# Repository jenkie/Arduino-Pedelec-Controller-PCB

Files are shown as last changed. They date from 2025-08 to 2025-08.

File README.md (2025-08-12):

# Arduino-Pedelec-Controller-PCB
PCB files for the Arduino Pedelec Controller

More info see http://www.pedelecforum.de/wiki/doku.php?id=elektrotechnik:forumscontroller

Shield: [][cc-by-nc]

This work is licensed under a
[Creative Commons Attribution-NonCommercial 4.0 International License][cc-by-nc].

[][cc-by-nc]

[cc-by-nc]: https://creativecommons.org/licenses/by-nc/4.0/
[cc-by-nc-image]: https://licensebuttons.net/l/by-nc/4.0/88x31.png
[cc-by-nc-shield]: https://img.shields.io/badge/License-CC%20BY--NC%204.0-lightgrey.svg

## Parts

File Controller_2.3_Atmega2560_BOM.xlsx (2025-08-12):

Part | Part Number | Quantity | Supplier
Housing | 1593LBK | 1 | Reichelt
Screws | SBL 29065-100 | 4 | Reichelt
Washers | 16 H 942 | 4 | Buerklin
RJ45-8X | 1401749 | 2 | Conrad
Connector 2-pol | PS 25/2G WS | 4 | Reichelt
Connector 3-Pol | PS 25/3G WS | 1
Connector 4-Pin | JST XH4P ST | 2 | Reichelt
Connector 4-Pin | 452408 | 2 | Pollin
Connector 5-Pol | PS 25/5G WS | 1 | Reichelt
ISP HDR 2x3 | SL 2X50G 2,54 | 1 | Reichelt
Buzzer | SUMMER AL-60P12 | 1 | Reichelt

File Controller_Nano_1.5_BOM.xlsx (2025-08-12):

Part | Description | Package | Part Number | Quantity | Supplier
Q3 | IRFS3107PBF | TO263 | IRFS3107PBF | 1 | Farnell
IC3 | LM2576HVS-ADJ | TO263-5 | 41 S 5413 | 1 | Buerklin
IC1 | ACS712 | SO-8 | 1651975 | 1 | Farnell
Pin header | 36 Pole |  | 59 F 6960 | 1 | Buerklin
RJ45 | RJ45-8X |  | 73 F 670 | 2 | Buerklin
U$1 | PIST-151 | PIST-151 | 74 D 4854 | 1 | Buerklin
IC2 | TLV1117-50CDCY 5V Regler | SOT223 | 1755288 | 1 | Farnell
R11 | 2K Trimmer | PVZ2A202A01B00 | PVZ2A202A01B00 | 1 | Farnell
D1 | SS3H10 | SMC | 1215109 | 1 | Farnell
T1 | IRFML8244TRPBF, FET | SOT-23 | 1857298 | 1 | Farnell
C2 | 100µF 63V | E3,5-8 | 12 D 5194 | 1 | Buerklin
C3 | 470 µF 16 V | E3,5-8 | 12 D 5114 | 1 | Buerklin
C4,9 | 100µF | E2-5 | 11 D 5300 | 2 | Buerklin
Q2 | NPN with hfe > 100 | SOT-23 | BC846B | 1 | Reichelt
R2,5,10,12,13 | 11k | R1206 | 1887478 | 5 | Farnell
C1,C10 | 10µF, 63V | E2-5 | 11 D 5346 | 2 | Buerklin
D2 | 20V/1A | DO-214AC | 1611257 | 1 | Farnell
R9 | 1.25k | R1206 | CRCW12061K20FKEA | 1 | Farnell
C5,8,11 | 1µF, 25V | C0805 | 1759429 | 3 | Farnell
R1 | 470K | R1206 | 1887522 | 1 | Farnell
R3,4,6 | 1k | R1206 | 2073877 | 3 | Farnell
C6,7 | 220n, >5V | C0805 | 1759173 | 2 | Farnell
D3 | Zener 12V | SOD323-W | MM3Z12VT1G | 1 | HBE
R8,15 | 150R | R1206 | 1100169 | 2 | Farnell
R18 | 150k | R1206 | 1100249 | 1 | Farnell
R7 | 820K | R1206 | 9337636 | 1 | Farnell
Screws | SBL 29065-100 |  | SBL 29065-100 | 4 | Reichelt
Housing | 1593LBK | Hammond | 1593LBK | 1 | Buerklin
Washers |  |  | 16 H 942 | 4 | Buerklin

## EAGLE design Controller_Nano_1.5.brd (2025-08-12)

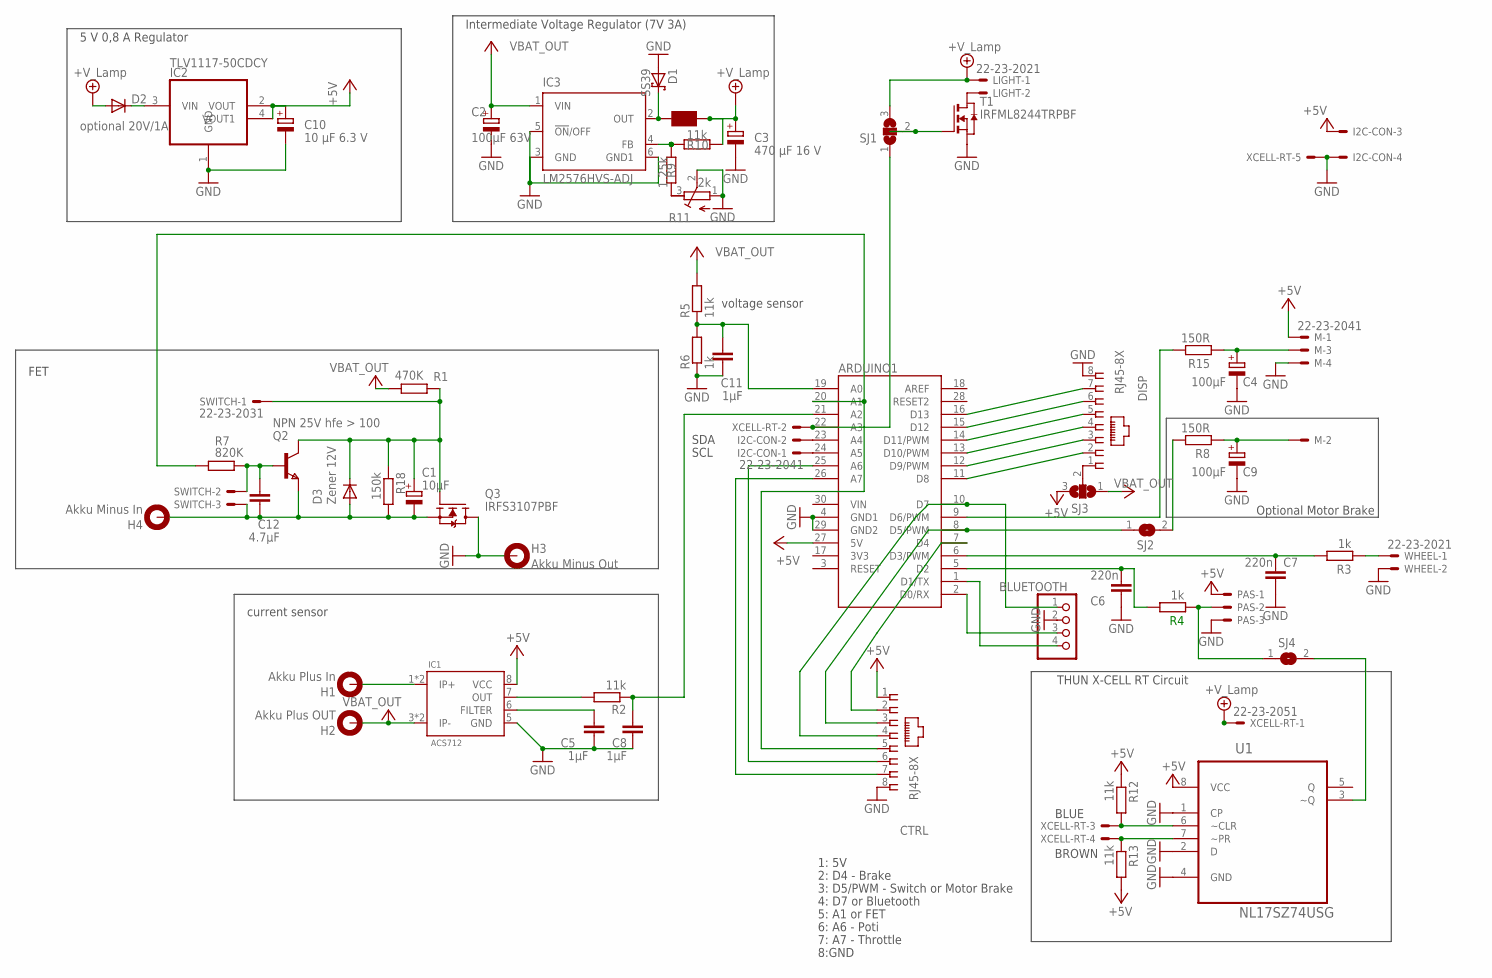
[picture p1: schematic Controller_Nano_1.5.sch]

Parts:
ARDUINO1: ARDUINO_NANO_CHECKED
BLUETOOTH: PINHD-1X4; 1X04
C1: 10µF; E2-5
C2: 100µF 63V; E3,5-8
C3: 470 µF 16 V; E3,5-8
C4, C9: 100µF; E2-5
C5, C8, C11: 1µF; C0805
C6, C7: 220n; C0805
C10: 10 µF 6.3 V; E2-5
C12: 4.7µF; C0805
CTRL: RJ45-8X; RJ45-NO-SHIELD
D1: SS39; SMC
D2: optional 20V/1A; DO-214AC
D3: Zener 12V; SOD323-W
DISP: RJ45-8X; RJ45-NO-SHIELD
H1: Akku Plus In; 2,8-PAD
H2: Akku Plus OUT; 2,8-PAD
H3: Akku Minus Out; 2,8-PAD
H4: Akku Minus In; 2,8-PAD
I2C-CON: 22-23-2041
IC1: ACS712; MARTIN-SMD-IC_SO-8
IC2: TLV1117-50CDCY; SOT223
IC3: LM2576HVS-ADJ; TO263-5
LIGHT: 22-23-2021; MPN 22-23-2021
M: 22-23-2041; MPN 22-23-2041
PAS: 22-23-2031
Q2: NPN 25V hfe > 100; SOT-23
Q3: IRFS3107PBF; TRANSISTOR-FET_TO263
R1: 470K; R1206
R2, R5, R10, R12, R13: 11k; R1206
R3, R4, R6: 1k; R1206
R7: 820K; R1206
R8, R15: 150R; R1206
R9: 1.25k; R1206
R11: 2k; RTRIM3103
R18: 150k; R1206
SJ1, SJ3: SJ2WW; SJ_2W
SJ2, SJ4: SJ
SWITCH: 22-23-2031; MPN 22-23-2031
T1: IRFML8244TRPBF; SOT-23
U1: NL17SZ74USG; SOP50P310X90-8N
U$1: PIST-151
WHEEL: 22-23-2021
XCELL-RT: 22-23-2051

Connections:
3V3: ARDUINO1.17 (3V3)
+5V: ARDUINO1.27 (5V), C10.+, CTRL.1, I2C-CON.3, IC1.8 (VCC), IC2.2 (VOUT), IC2.4 (VOUT1), M.1, PAS.1, R12.1, R13.2, SJ3.3, U1.8 (VCC)
+5V/2: C3.+, D2.A, LIGHT.1, R10.1, SJ1.3, U$1.P$2, XCELL-RT.1
GND: ARDUINO1.4 (GND1), ARDUINO1.29 (GND2), BLUETOOTH.2, C2.-, C3.-, C4.-, C5.2, C6.2, C7.2, C8.2, C9.-, C10.-, C11.2, CTRL.8, D1.A, DISP.8, H3.B2,8, I2C-CON.4, IC1.5 (GND), IC2.1 (GND), IC3.3 (GND), IC3.5 (!ON!/OFF), IC3.6 (GND1), M.4, PAS.3, Q3.2D (D), R6.1, R11.1 (E), R11.2 (S), T1.2 (S), U1.1 (CP), U1.2 (D), U1.4 (GND), WHEEL.2, XCELL-RT.5
unnamed: ARDUINO1.24 (A5), I2C-CON.1
unnamed: ARDUINO1.23 (A4), I2C-CON.2
unnamed: ARDUINO1.20 (A1), CTRL.5, R7.2
unnamed: ARDUINO1.16 (D13), DISP.7
unnamed: ARDUINO1.15 (D12), DISP.6
unnamed: ARDUINO1.14 (D11/PWM), DISP.5
unnamed: ARDUINO1.13 (D10/PWM), DISP.4
unnamed: ARDUINO1.12 (D9/PWM), DISP.3
unnamed: ARDUINO1.9 (D6/PWM), R15.2
unnamed: IC3.4 (FB), R9.2, R10.2
unnamed: LIGHT.2, T1.1 (D)
unnamed: C1.-, C12.2, D3.A, H4.B2,8, Q2.2 (E), Q3.3S (S), R18.2, SWITCH.3
unnamed: C1.+, D3.C, Q2.1 (C), Q3.1G (G), R1.2, R18.1, SWITCH.1
unnamed: R3.1, WHEEL.1
unnamed: D1.C, IC3.2 (OUT), U$1.P$1
unnamed: C5.1, IC1.6 (FILTER)
unnamed: ARDUINO1.19 (A0), C11.1, R5.1, R6.2
unnamed: ARDUINO1.22 (A3), SJ1.1, XCELL-RT.2
unnamed: ARDUINO1.7 (D4), CTRL.2
unnamed: ARDUINO1.8 (D5/PWM), CTRL.3, SJ2.1
unnamed: ARDUINO1.10 (D7), BLUETOOTH.1, CTRL.4
unnamed: C12.1, Q2.3 (B), R7.1, SWITCH.2
unnamed: ARDUINO1.11 (D8), DISP.2
unnamed: ARDUINO1.5 (D2), C6.1, R4.2
unnamed: IC1.7 (OUT), R2.2
unnamed: ARDUINO1.2 (D0/RX), BLUETOOTH.3
unnamed: ARDUINO1.25 (A6), CTRL.6
unnamed: ARDUINO1.26 (A7), CTRL.7
unnamed: ARDUINO1.1 (D1/TX), BLUETOOTH.4
unnamed: C9.+, M.2, R8.1
unnamed: C4.+, M.3, R15.1
unnamed: PAS.2, R4.1, SJ4.1
unnamed: ARDUINO1.6 (D3/PWM), C7.1, R3.2
unnamed: DISP.1, SJ3.2
unnamed: ARDUINO1.21 (A2), C8.1, R2.1
unnamed: SJ1.2, T1.3 (G)
unnamed: D2.C, IC2.3 (VIN)
unnamed: R8.2, SJ2.2
unnamed: R9.1, R11.3 (A)
unnamed: R12.2, U1.6 (~CLR), XCELL-RT.3
unnamed: R13.1, U1.7 (~PR), XCELL-RT.4
unnamed: SJ4.2, U1.3 (~Q)
VBAT_IN: H1.B2,8, IC1.1 (IP+), IC1.2 (IP+)
VBAT_OUT: C2.+, H2.B2,8, IC1.3 (IP-), IC1.4 (IP-), IC3.1 (VIN), R1.1, R5.2, SJ3.1

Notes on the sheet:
voltage sensor
current sensor
Intermediate Voltage Regulator (7V 3A)
1: 5V
2: D4 - Brake
3: D5/PWM - Switch or Motor Brake
4: D7 or Bluetooth
5: A1 or FET
6: A6 - Poti
7: A7 - Throttle
8:GND
SDA
SCL
FET
Optional Motor Brake
5 V 0,8 A Regulator
BLUE
BROWN
THUN X-CELL RT Circuit

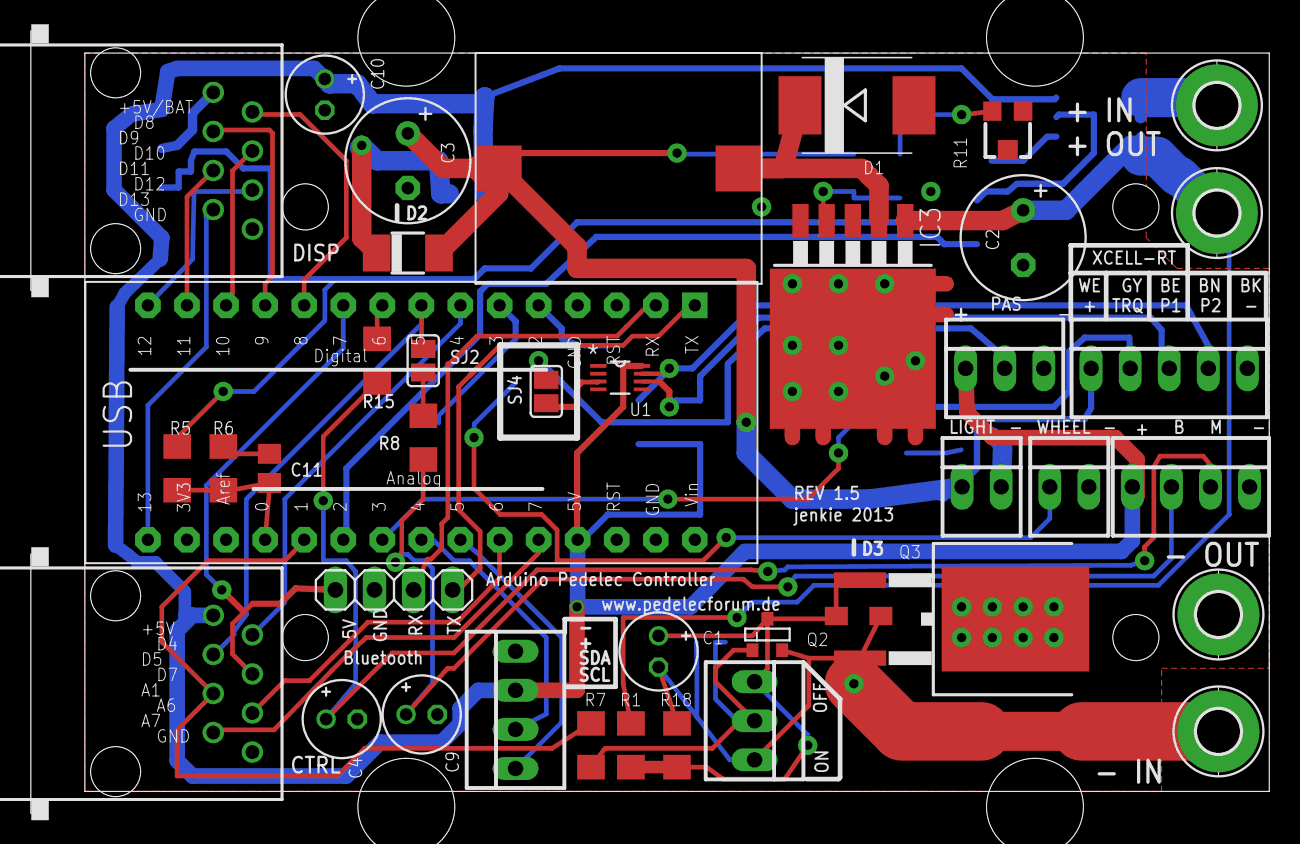
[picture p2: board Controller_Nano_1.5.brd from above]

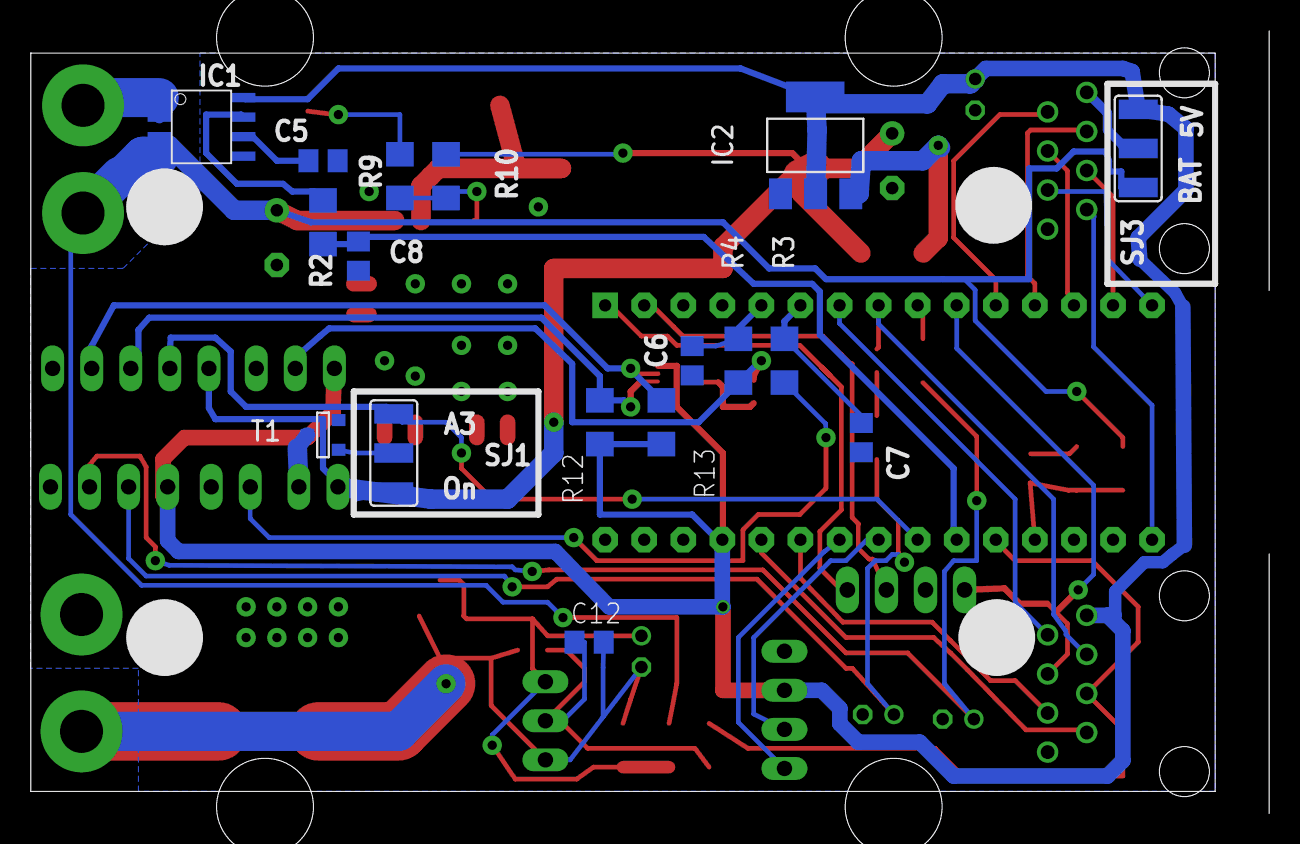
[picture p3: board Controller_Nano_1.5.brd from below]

Board: 2 copper layers, 80.5 x 50.9 mm, 58 parts (17 on the bottom side), 47 nets.

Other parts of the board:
U$2: 1593L

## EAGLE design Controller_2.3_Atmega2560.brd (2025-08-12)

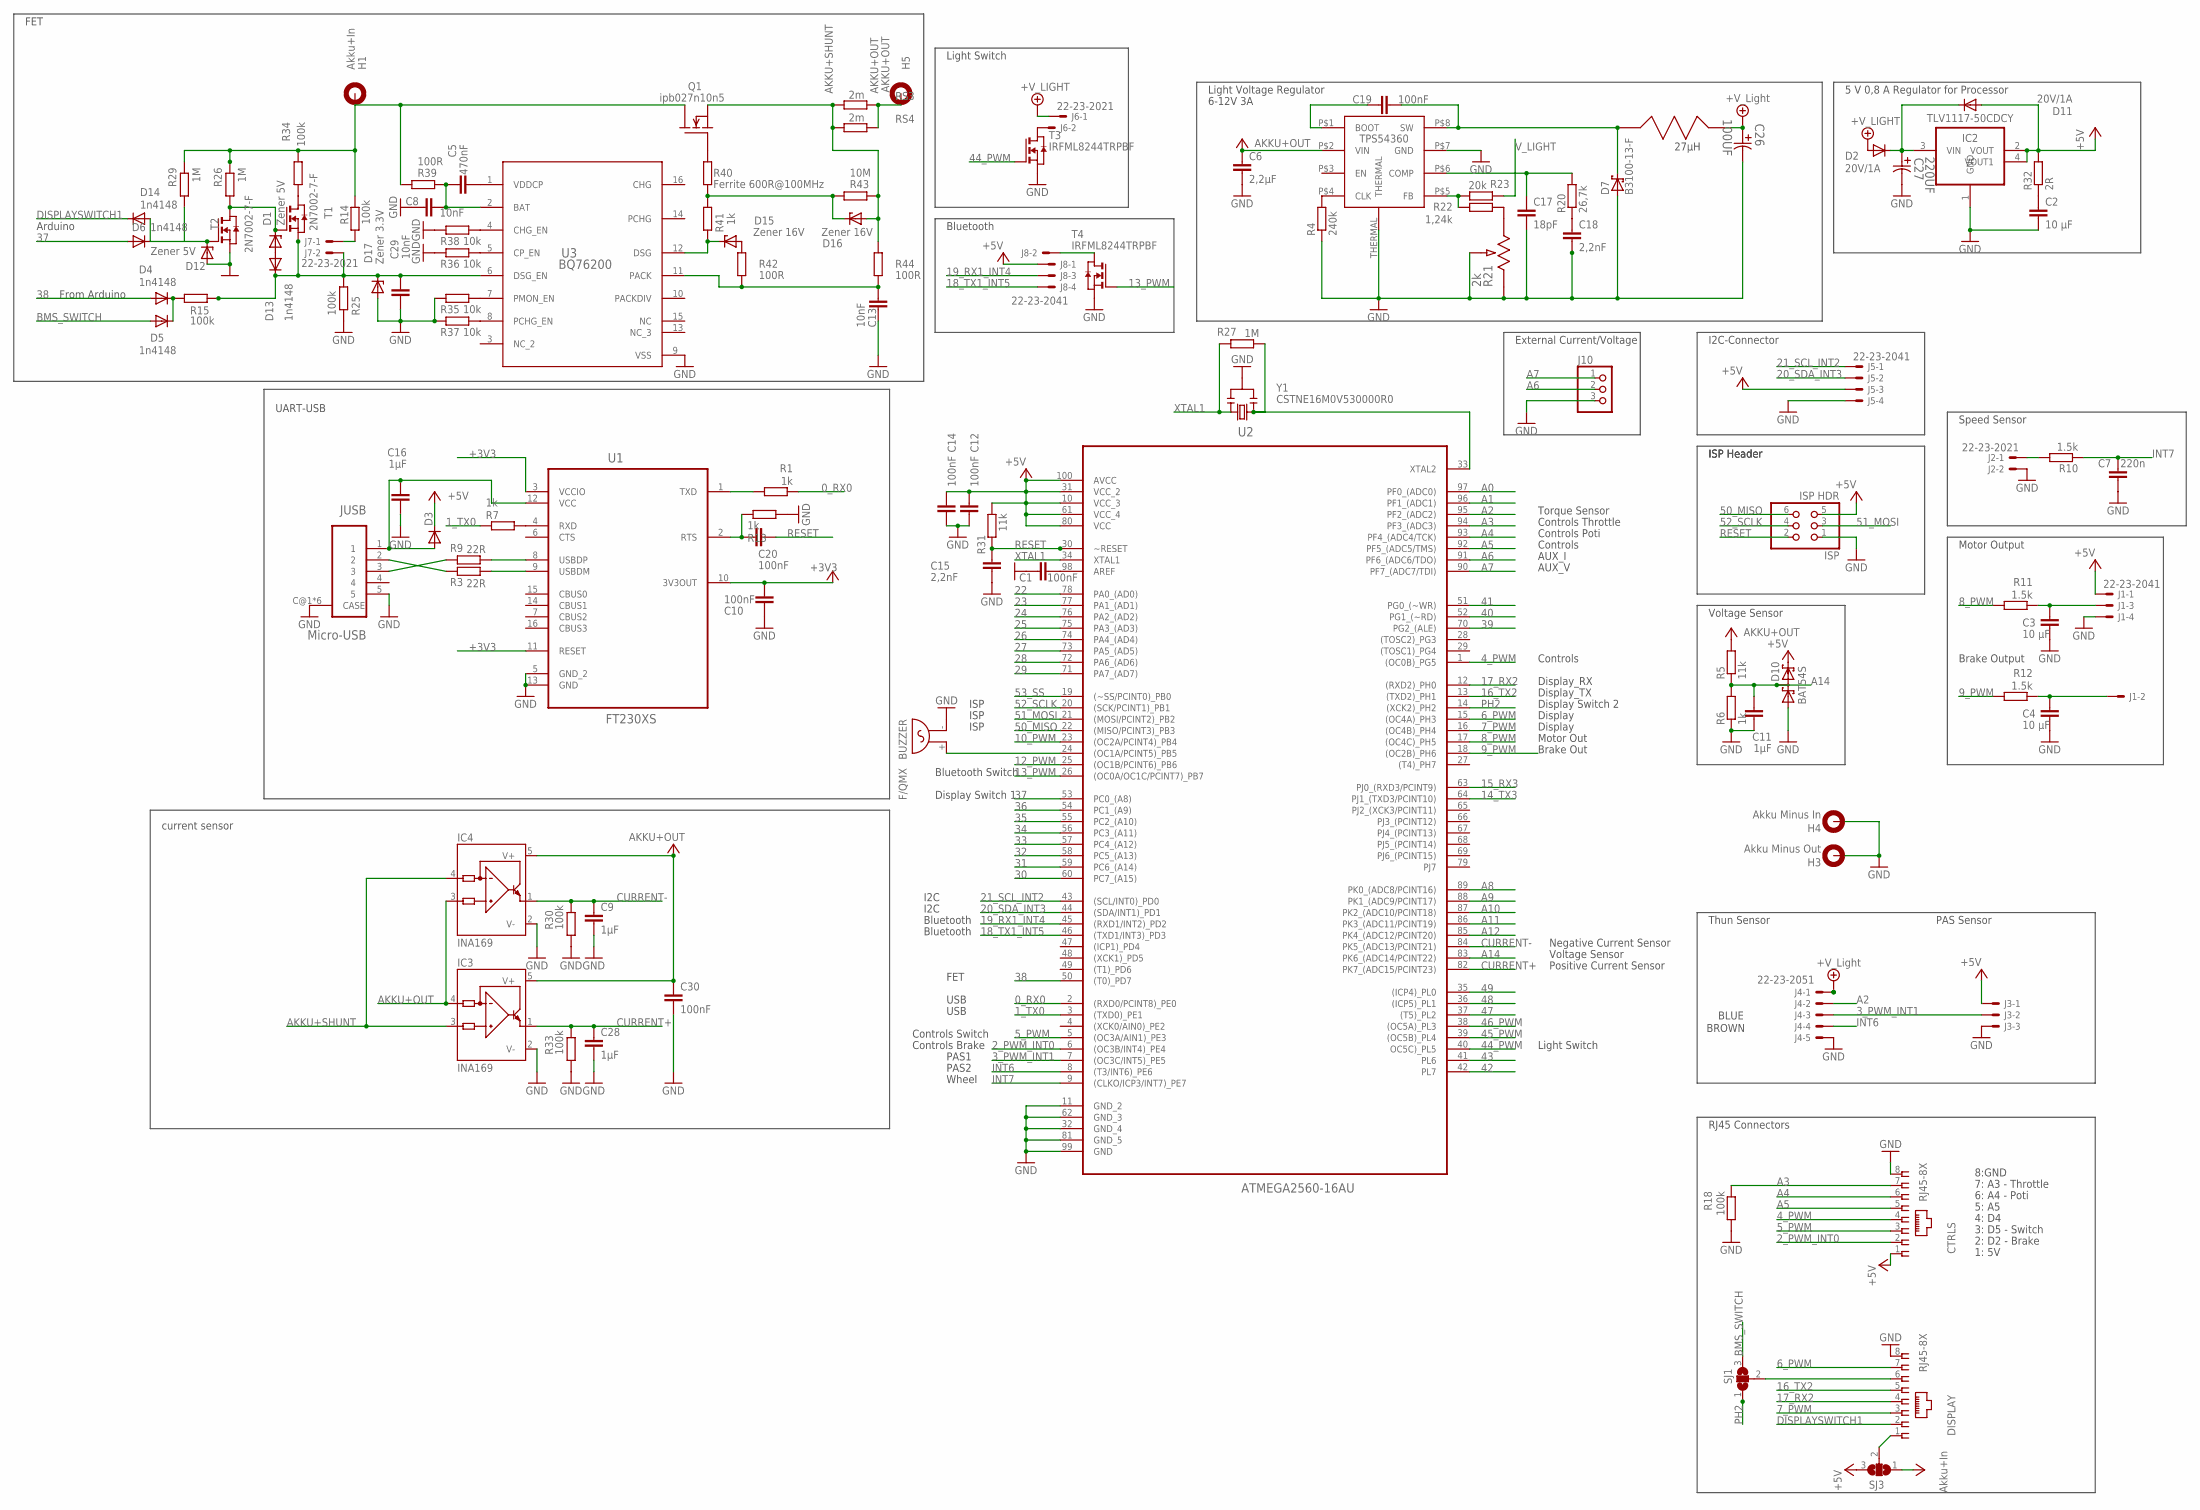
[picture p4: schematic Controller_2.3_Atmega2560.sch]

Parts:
BUZZER: F/QMX
C1, C10, C12, C14, C19, C20, C30: 100nF; C0603
C2, C3, C4: 10 µF; C1206
C5: 470nF; C0603
C6: 2,2µF; C1210
C7: 220n; C0603
C8, C13, C29: 10nF; C0603
C9, C11, C16, C28: 1µF; C0603
C15, C18: 2,2nF; C0603
C17: 18pF; C0603
C26: 100UF; CAPAE660X800N
C27: 220UF; CAPAE660X800N
CTRLS: RJ45-8X; RJ45-NO-SHIELD
D1, D12: Zener 5V; SOD323-W
D2, D3, D11: 20V/1A; DO-214AC
D4, D5, D6, D13, D14: 1n4148; SOD323-W
D7: B3100-13-F; SMC
D10: BAT54S; SOT23
D15, D16: Zener 16V; SOD323-W
D17: Zener 3.3V; SOD323-W
DISPLAY: RJ45-8X; RJ45-NO-SHIELD
H1: Akku+In; 2,8-PAD
H3: Akku Minus Out; 2,8-PAD
H4: Akku Minus In; 2,8-PAD
H5: AKKU+OUT; 2,8-PAD
IC2: TLV1117-50CDCY; SOT223
IC3, IC4: INA169; SOT23-5
ISP: ISP HDR; 2X03
J1: 22-23-2041; MPN 22-23-2041
J2, J7: 22-23-2021
J3: 22-23-2031
J4: 22-23-2051
J5, J8: 22-23-2041
J6: 22-23-2021; MPN 22-23-2021
J10: PINHD-1X3; 1X03
JUSB: Micro-USB; MOLEX_47346-0001
Q1: ipb027n10n5; D2PAK
R1, R6, R7, R13, R41: 1k; R0603
R3, R9: 22R; R0603
R4: 240k; R0603
R5, R31: 11k; R0603
R10, R11, R12: 1.5k; R0603
R14, R15, R18, R25, R30, R33, R34: 100k; R0603
R20: 26,7k; R0603
R21: 2k; POT_EVM3W
R22: 1,24k; R0603
R23: 20k; R0603
R26, R27, R29: 1M; R0603
R32: 2R; R0603
R35, R36, R37, R38: 10k; R0603
R39, R42, R44: 100R; R0603
R40: Ferrite 600R@100MHz; R0603
R43: 10M; R0603
RS3, RS4: 2m; R2512
SJ1, SJ3: SJ2W; SJ_2
T1, T2: 2N7002-7-F; SOT-23
T3, T4: IRFML8244TRPBF; SOT-23
U1: FT230XS; SOP63P600X175-16N
U2: ATMEGA2560-16AU; QFP50P1600X1600X120-100N
U3: BQ76200; PW0016A_N
U9: SRR1260-270M; ARR1260
U11: TPS54360; R-PDSO-G8
Y1: CSTNE16M0V530000R0; RESONATOR

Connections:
0_RX0: R1.1, U2.2 ((RXD0/PCINT8)_PE0)
1_TX0: R7.1, U2.3 ((TXD0)_PE1)
2_PWM_INT0: CTRLS.2, U2.6 ((OC3B/INT4)_PE4)
3_PWM_INT1: J3.2, J4.3, U2.7 ((OC3C/INT5)_PE5)
4_PWM: CTRLS.4, U2.1 ((OC0B)_PG5)
5_PWM: CTRLS.3, U2.5 ((OC3A/AIN1)_PE3)
6_PWM: DISPLAY.7, U2.15 ((OC4A)_PH3)
7_PWM: DISPLAY.3, U2.16 ((OC4B)_PH4)
8_PWM: R11.2, U2.17 ((OC4C)_PH5)
9_PWM: R12.2, U2.18 ((OC2B)_PH6)
10_PWM: U2.23 ((OC2A/PCINT4)_PB4)
12_PWM: U2.25 ((OC1B/PCINT6)_PB6)
13_PWM: T4.3 (G), U2.26 ((OC0A/OC1C/PCINT7)_PB7)
14_TX3: U2.64 (PJ1_(TXD3/PCINT10))
15_RX3: U2.63 (PJ0_(RXD3/PCINT9))
16_TX2: DISPLAY.5, U2.13 ((TXD2)_PH1)
17_RX2: DISPLAY.4, U2.12 ((RXD2)_PH0)
18_TX1_INT5: J8.4, U2.46 ((TXD1/INT3)_PD3)
19_RX1_INT4: J8.3, U2.45 ((RXD1/INT2)_PD2)
20_SDA_INT3: J5.2, U2.44 ((SDA/INT1)_PD1)
21_SCL_INT2: J5.1, U2.43 ((SCL/INT0)_PD0)
22: U2.78 (PA0_(AD0))
23: U2.77 (PA1_(AD1))
24: U2.76 (PA2_(AD2))
25: U2.75 (PA3_(AD3))
26: U2.74 (PA4_(AD4))
27: U2.73 (PA5_(AD5))
28: U2.72 (PA6_(AD6))
29: U2.71 (PA7_(AD7))
30: U2.60 (PC7_(A15))
31: U2.59 (PC6_(A14))
32: U2.58 (PC5_(A13))
33: U2.57 (PC4_(A12))
34: U2.56 (PC3_(A11))
35: U2.55 (PC2_(A10))
36: U2.54 (PC1_(A9))
37: D6.A, U2.53 (PC0_(A8))
38: D4.A, U2.50 ((T0)_PD7)
39: U2.70 (PG2_(ALE))
40: U2.52 (PG1_(~RD))
41: U2.51 (PG0_(~WR))
42: U2.42 (PL7)
43: U2.41 (PL6)
44_PWM: T3.3 (G), U2.40 (OC5C)_PL5)
45_PWM: U2.39 ((OC5B)_PL4)
46_PWM: U2.38 ((OC5A)_PL3)
47: U2.37 ((T5)_PL2)
48: U2.36 ((ICP5)_PL1)
49: U2.35 ((ICP4)_PL0)
50_MISO: ISP.6, U2.22 ((MISO/PCINT3)_PB3)
51_MOSI: ISP.3, U2.21 ((MOSI/PCINT2)_PB2)
52_SCLK: ISP.4, U2.20 ((SCK/PCINT1)_PB1)
53_SS: U2.19 ((~SS/PCINT0)_PB0)
+3V3: C10.2, U1.3 (VCCIO), U1.10 (3V3OUT), U1.11 (RESET)
+5V: C12.2, C14.2, CTRLS.1, D3.C, D10.2 (C2), D11.A, IC2.2 (VOUT), IC2.4 (VOUT1), ISP.5, J1.1, J3.1, J5.3, J8.1, R31.2, R32.2, SJ3.3, U2.10 (VCC_3), U2.31 (VCC_2), U2.61 (VCC_4), U2.80 (VCC), U2.100 (AVCC)
A0: U2.97 (PF0_(ADC0))
A1: U2.96 (PF1_(ADC1))
A2: J4.2, U2.95 (PF2_(ADC2))
A3: CTRLS.7, R18.1, U2.94 (PF3_(ADC3))
A4: CTRLS.6, U2.93 (PF4_(ADC4/TCK))
A5: CTRLS.5, U2.92 (PF5_(ADC5/TMS))
A6: J10.2, U2.91 (PF6_(ADC6/TDO))
A7: J10.1, U2.90 (PF7_(ADC7/TDI))
A8: U2.89 (PK0_(ADC8/PCINT16))
A9: U2.88 (PK1_(ADC9/PCINT17))
A10: U2.87 (PK2_(ADC10/PCINT18))
A11: U2.86 (PK3_(ADC11/PCINT19))
A12: U2.85 (PK4_(ADC12/PCINT20))
A14: C11.1, D10.3 (C1A2), R5.1, R6.2, U2.83 (PK6_(ADC14/PCINT22))
AKKU+IN: H1.B2,8, Q1.2 (D), R14.2, R26.1, R29.1, R34.1, R39.2, SJ3.1
AKKU+OUT: C6.1, C30.1, H5.B2,8, IC3.4 (IN-), IC3.5 (V+), IC4.3 (IN+), IC4.5 (V+), R5.2, RS3.2, RS4.2, U11.P$2 (VIN)
AKKU+SHUNT: D16.A, IC3.3 (IN+), IC4.4 (IN-), Q1.3 (S), R43.1, R44.2, RS3.1, RS4.1
BMS_SWITCH: D5.A, SJ1.3
CURRENT+: C28.1, IC3.1 (OUT), R33.2, U2.82 (PK7_(ADC15/PCINT23))
CURRENT-: C9.1, IC4.1 (OUT), R30.2, U2.84 (PK5_(ADC13/PCINT21))
DISPLAYSWITCH1: D14.C, DISPLAY.2
GND: BUZZER.- (1), C1.2, C2.2, C3.2, C4.2, C6.2, C7.2, C8.1, C9.2, C10.1, C11.2, C12.1, C13.1, C14.1, C15.2, C16.2, C17.2, C18.2, C26.2, C27.2, C28.2, C29.1, C30.2, CTRLS.8, D7.A, D10.1 (A1), D12.A, D17.A, DISPLAY.8, H3.B2,8, H4.B2,8, IC2.1 (GND), IC3.2 (V-), IC4.2 (V-), ISP.1, J1.4, J2.2, J3.3, J4.5, J5.4, J10.3, JUSB.5, JUSB.C@1 (CASE), JUSB.C@2 (CASE), JUSB.C@3 (CASE), JUSB.C@4 (CASE), JUSB.C@5 (CASE), JUSB.C@6 (CASE), R4.1, R6.1, R13.2, R18.2, R21.1, R21.2, R25.1, R30.1, R33.1, R35.2, R36.2, R37.2, R38.2, T2.2 (S), T3.2 (S), T4.2 (S), U1.5 (GND_2), U1.13 (GND), U2.11 (GND_2), U2.32 (GND_4), U2.62 (GND_3), U2.81 (GND_5), U2.99 (GND), U3.9 (VSS), U11.P$7 (GND), U11.THERMAL, Y1.2
INT6: J4.4, U2.8 ((T3/INT6)_PE6)
INT7: C7.1, R10.1, U2.9 ((CLKO/ICP3/INT7)_PE7)
unnamed: J6.2, T3.1 (D)
unnamed: R4.2, U11.P$4 (CLK)
unnamed: C16.1, D3.A, JUSB.1, U1.12 (VCC)
unnamed: C1.1, U2.98 (AREF)
unnamed: J8.2, T4.1 (D)
unnamed: C20.1, R13.1, U1.2 (RTS)
unnamed: R3.1, U1.9 (USBDM)
unnamed: R9.1, U1.8 (USBDP)
unnamed: R1.2, U1.1 (TXD)
unnamed: JUSB.2, R3.2
unnamed: C2.1, R32.1
unnamed: R7.2, U1.4 (RXD)
unnamed: R21.3, R22.1
unnamed: J2.1, R10.2
unnamed: JUSB.3, R9.2
unnamed: D1.A, D13.A
unnamed: C18.1, R20.1
unnamed: C17.1, R20.2, U11.P$6 (COMP)
unnamed: BUZZER.+ (2), U2.24 ((OC1A/PCINT5)_PB5)
unnamed: R34.2, T1.1 (D)
unnamed: R37.1, U3.8 (PCHG_EN)
unnamed: R22.2, R23.2, U11.P$5 (FB)
unnamed: D4.C, D5.C, R15.1
unnamed: R35.1, U3.7 (PMON_EN)
unnamed: C3.1, J1.3, R11.1
unnamed: C4.1, J1.2, R12.1
unnamed: C19.2, D7.C, U9.P$1, U11.P$8 (SW)
unnamed: DISPLAY.1, SJ3.2
unnamed: J7.1, R14.1
unnamed: C27.1, D2.C, D11.C, IC2.3 (VIN)
unnamed: R36.1, U3.5 (CP_EN)
unnamed: R38.1, U3.4 (CHG_EN)
unnamed: C5.2, U3.1 (VDDCP)
unnamed: D1.C, R26.2, T1.3 (G), T2.1 (D)
unnamed: C19.1, U11.P$1 (BOOT)
unnamed: C5.1, C8.2, R39.1, U3.2 (BAT)
unnamed: C29.2, D13.C, D17.C, J7.2, R15.2, R25.2, T1.2 (S), U3.6 (DSG_EN)
unnamed: DISPLAY.6, SJ1.2
unnamed: D15.A, R42.2
unnamed: D6.C, D12.C, D14.A, R29.2, T2.3 (G)
unnamed: C13.2, R42.1, R44.1, U3.11 (PACK)
unnamed: Q1.1 (G), R40.2
unnamed: D16.C, R40.1, R41.2, R43.2
unnamed: D15.C, R41.1, U3.12 (DSG)
unnamed: R27.1, U2.33 (XTAL2), Y1.1
PH2: SJ1.1, U2.14 ((XCK2)_PH2)
RESET: C15.1, C20.2, ISP.2, R31.1, U2.30 (~RESET)
V_LIGHT: C26.1, D2.A, J4.1, J6.1, R23.1, U9.P$2
XTAL1: R27.2, U2.34 (XTAL1), Y1.3

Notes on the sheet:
Voltage Sensor
current sensor
1: 5V
2: D2 - Brake
3: D5 - Switch
4: D4
5: A5
6: A4 - Poti
7: A3 - Throttle
8:GND
FET
5 V 0,8 A Regulator for Processor
BLUE
BROWN
ISP Header
I2C-Connector
Thun Sensor
PAS Sensor
Speed Sensor
Light Voltage Regulator
6-12V 3A
Motor Output
Brake Output
Light Switch
RJ45 Connectors
27µH
UART-USB
PAS1
PAS2
Bluetooth
USB
Bluetooth Switch
Positive Current Sensor
Torque Sensor
Wheel
Motor Out
Brake Out
Display_RX
Display_TX
Display Switch 2

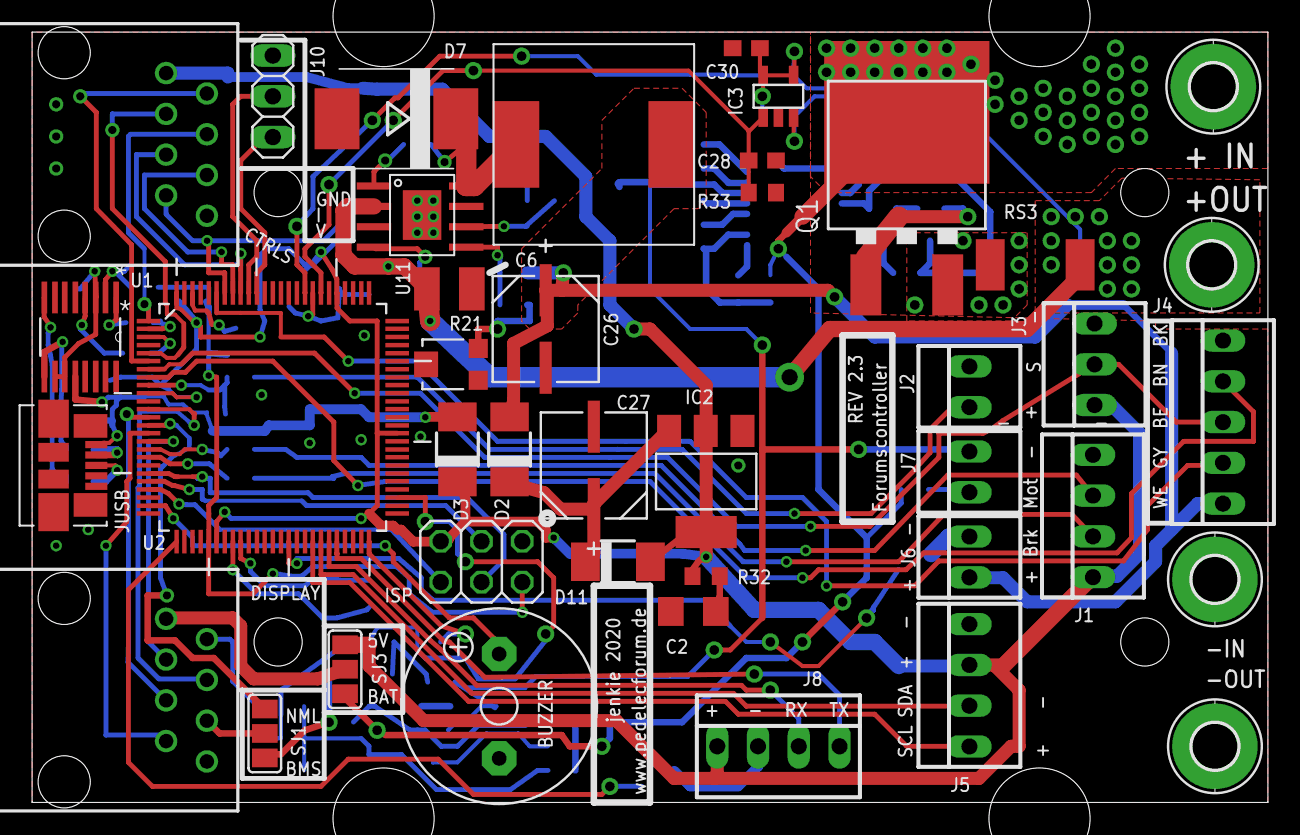
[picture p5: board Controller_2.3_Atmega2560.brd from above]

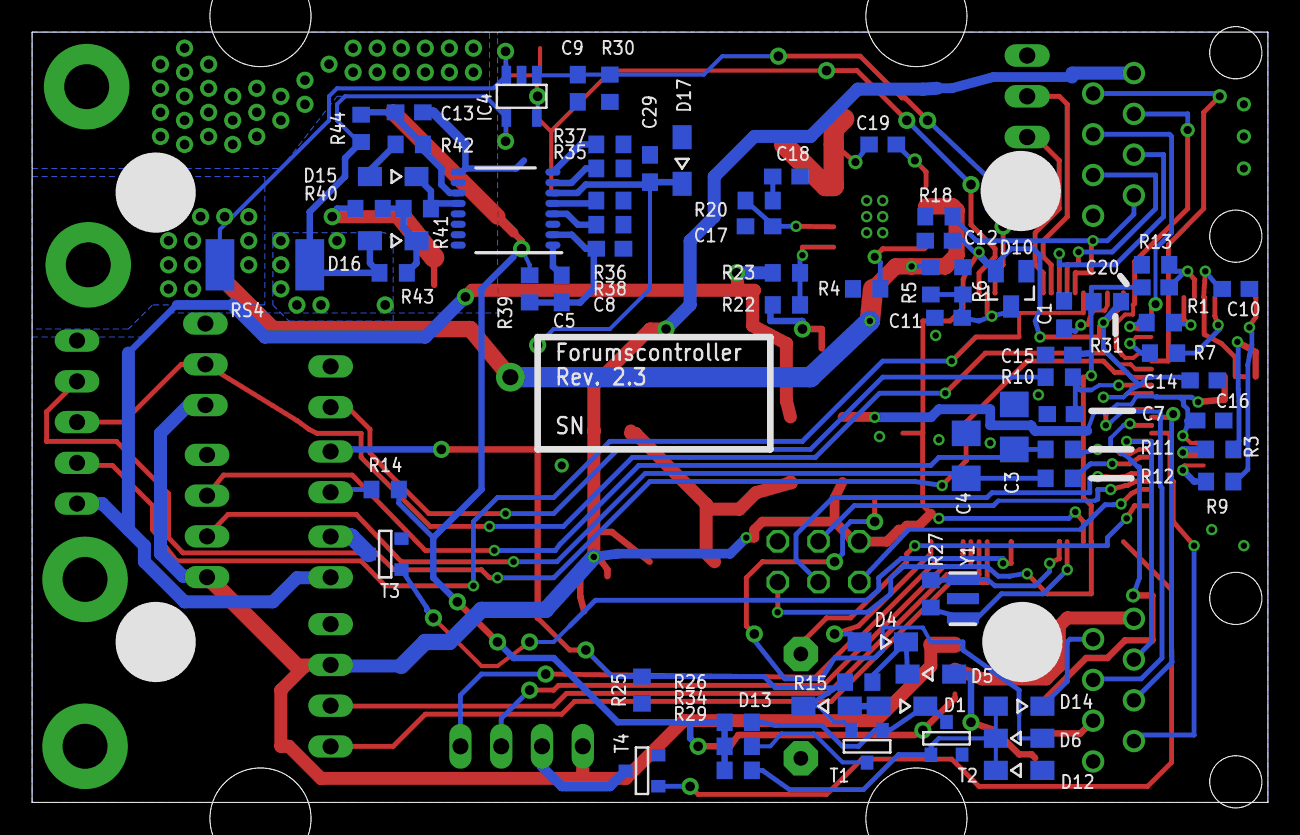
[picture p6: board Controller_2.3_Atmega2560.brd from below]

Board: 2 copper layers, 77.0 x 48.0 mm, 114 parts (72 on the bottom side), 91 nets.

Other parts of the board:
U$2: 1593L

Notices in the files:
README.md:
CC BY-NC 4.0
